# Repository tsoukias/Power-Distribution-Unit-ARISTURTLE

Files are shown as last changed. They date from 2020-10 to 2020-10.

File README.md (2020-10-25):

# Power Distribution Unit for Aristotle University Racing Team Electric (ARISTURTLE)

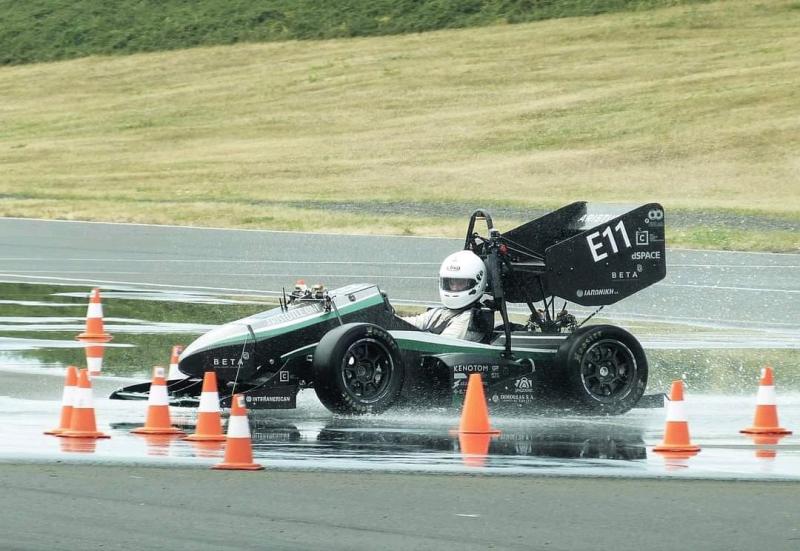
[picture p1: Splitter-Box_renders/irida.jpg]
<p align= "center">`</p>

In this repository anyone can found all the CAD files for the power distribution unit / splitter box used by ARISTURTLE in the electric racing car of 2017-2018, called Irida. This project was made in collaboration with Iakovos Koutris. 

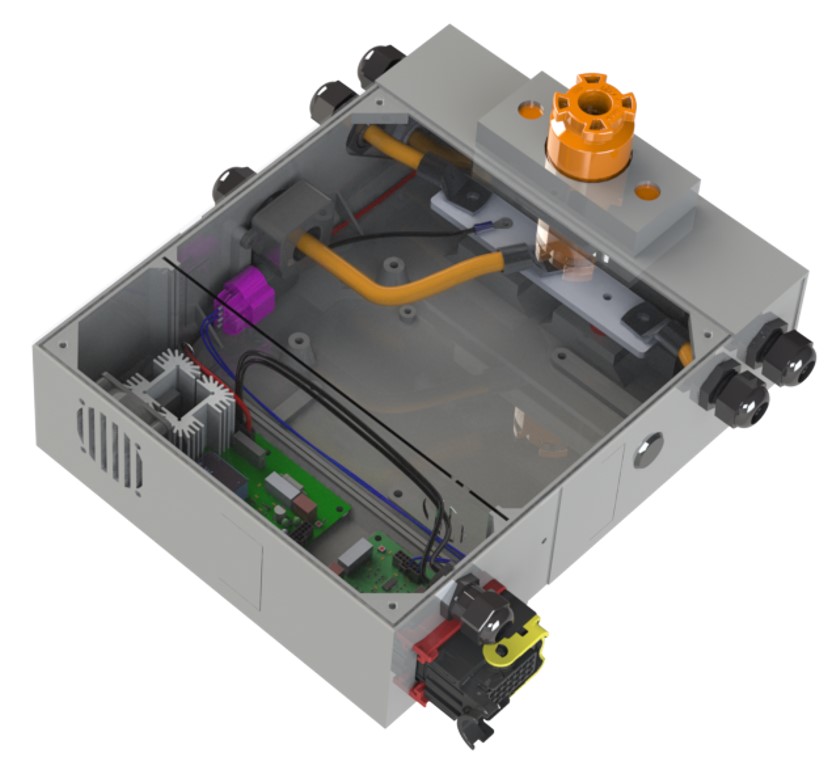
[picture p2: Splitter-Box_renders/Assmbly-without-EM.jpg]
<p align= "center">`</p>

### Brief Explanation

The power distribution unit is a *3D-printed box*, containing all the necessary connections for splitting the *DC High Voltage* from the battery of the racecar in order to supply the two inverters of the car, by splitting the positive and negative pole to two supply lines. It also contains the **discharge circuit** for the DC link capacitors of the inverters the **BSPD** (Brake System Plausibility Device), the **energy meter** for the Formula Student competitions and the **HVD** (High Voltage Disconnect). Below you can see the **powertrain** of the racecar. The top container is the *power distribution unit*.

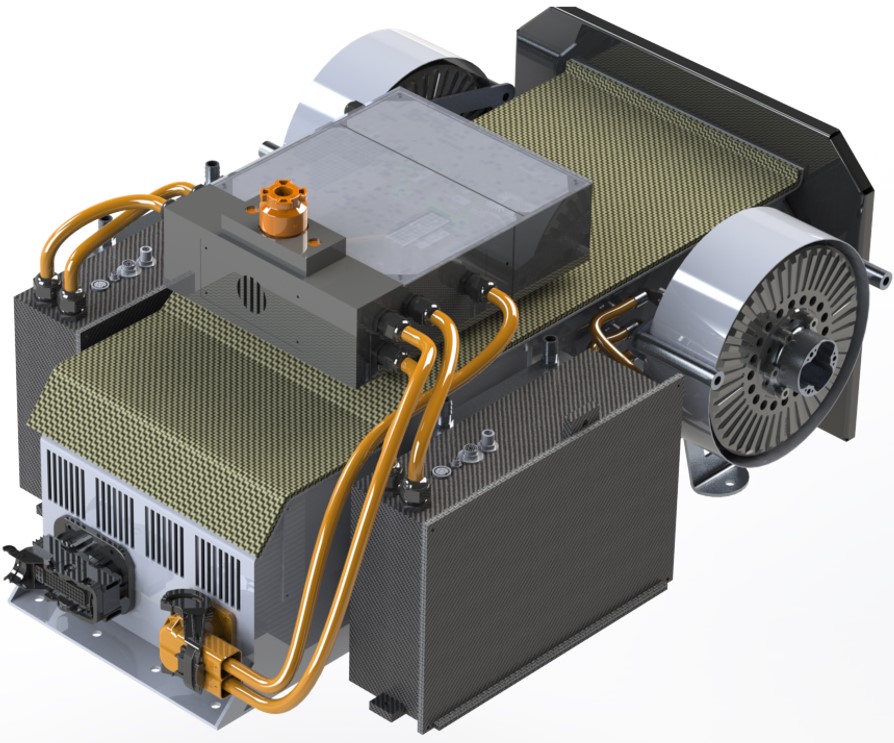
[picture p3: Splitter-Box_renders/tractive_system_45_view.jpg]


### Structural 

The power distribution unit is *3D-printed*, thing that gives facility for many configurations. The construction is composed of 6 pieces, due to the 3D printer restrictions, that were glued together. The box is made of ABS, due to its low weight, its high temperature resistance and because its electrically non conductive. An exploded view of the splitter box as well as the HVD lid can be seen below. The top lid of the box is a 2mm transparent polycarbonate piece for fast inspection of the system.  

| Splitter Box Exploded | HVD Lid |
| :---: | :---: |
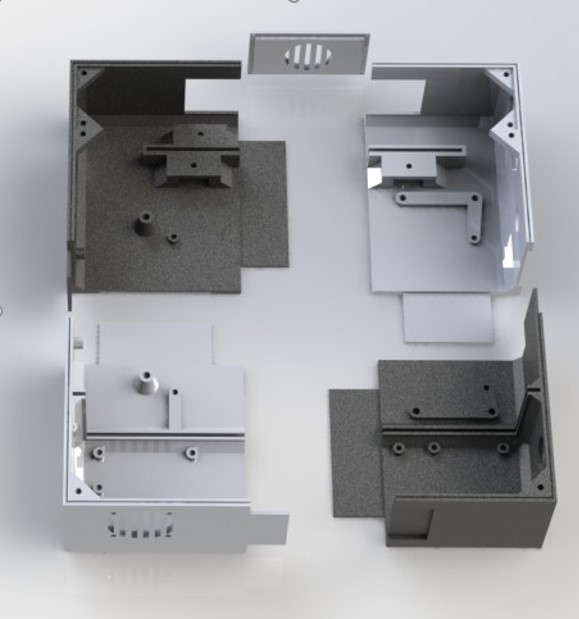
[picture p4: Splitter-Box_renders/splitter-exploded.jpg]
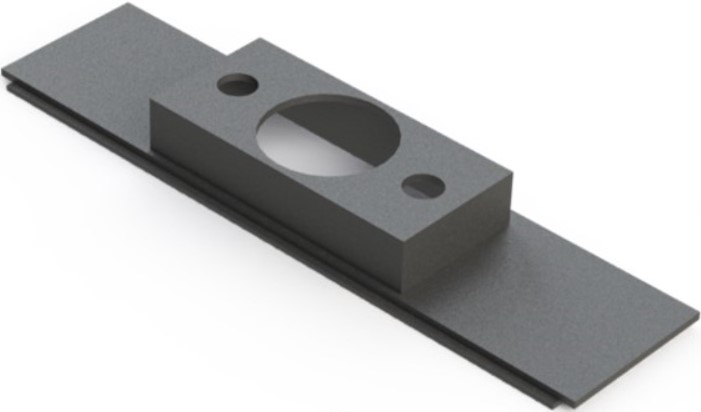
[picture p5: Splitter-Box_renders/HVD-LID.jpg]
|  |  |

For waterproofing the construction a special recess was placed around the perimeter of the box for installing an o-ring. The box has two compartments that are separated by a polycarbonate piece for ensuring electrical insulation between the two. One other important aspect of the construction is the use of brass threaded inserts for screwing all the components together. These were fitted to ABS via a soldering iron. Lastly, for ensuring proper installation for the High Voltage path threaded insulators were used. 

| Brass Threaded Insert | Threaded Insulators |
| :---: | :---: |
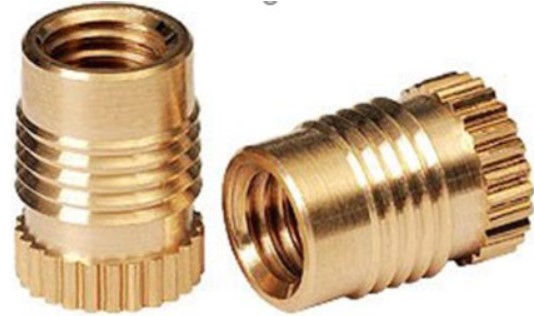
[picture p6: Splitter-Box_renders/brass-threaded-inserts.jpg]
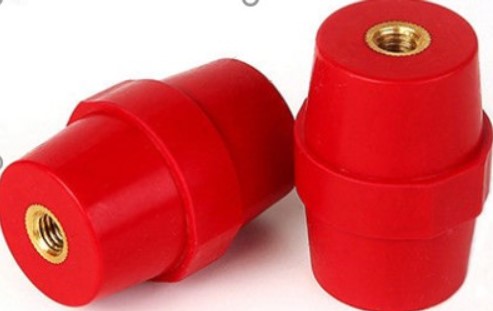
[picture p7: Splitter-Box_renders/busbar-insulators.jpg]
|  |  |

### High Voltage Compartment

The High Voltage compartment features the two nodes where the positive and negative terminal of the battery split, the HVD, the Energy Meters & also topologies for current and voltage measurements. The nodes can be seen below for each terminal:

| HV+ busbar | HV- busbar |
| :---: | :---: |
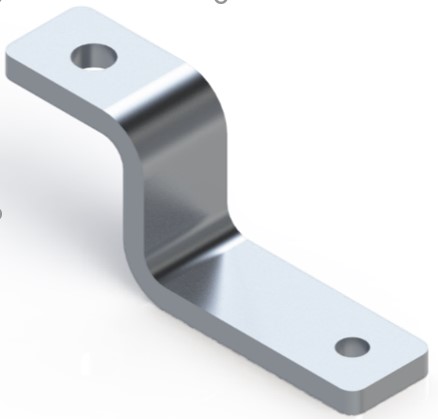
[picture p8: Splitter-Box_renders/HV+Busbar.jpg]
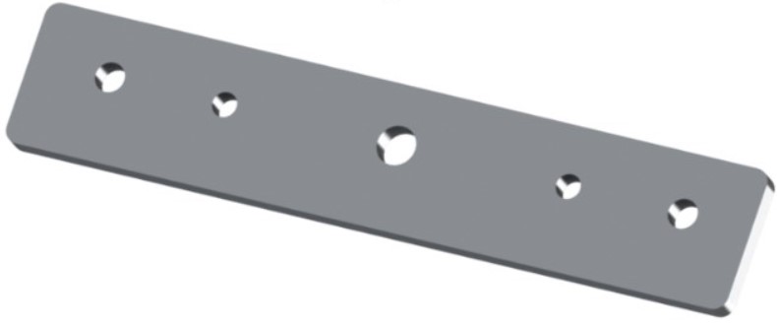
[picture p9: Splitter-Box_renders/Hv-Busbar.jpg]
|  |  |

The HVD is placed in the front part of the box, right in the center. It is contained inside a lid, that is mounted on the top of the box, and is mounted in the outside skin of the chassis with two M8 bolts. 

Two cables from the accumulator container are inserting the splitter box from the left side through PG13.5 cable glands as shown in the picture.

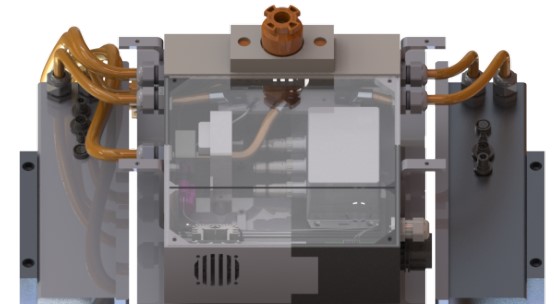
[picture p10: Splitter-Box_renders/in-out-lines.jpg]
<p align= "center">`</p>

The positive line is connected to the one side of the HVD with a 35M8 ring terminal. The other side of the HVD is where the split takes place, as an S shaped HV+ busbar and a 25M8 ring terminal is connected there. The busbar is then connected to a 25M6 ring terminal and the cable exits the splitter box from the left side through a cable gland, while the other cable exits from the right side. 

The negative line passes through a LEM that is mounted in the side of the box and is connected in the middle of the HV- busbar with a 35M8 ring terminal. Then from the end of each side, a 25M6 ring terminal is connected and the cables are exiting the splitter box through PG 13.5 cable glands.

| Cable gland | Ring Terminal |
| :---: | :---: |
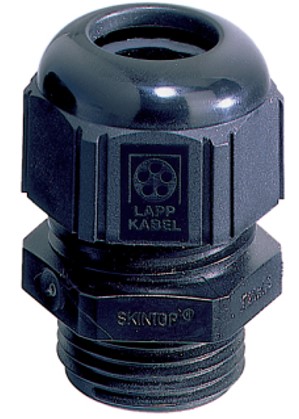
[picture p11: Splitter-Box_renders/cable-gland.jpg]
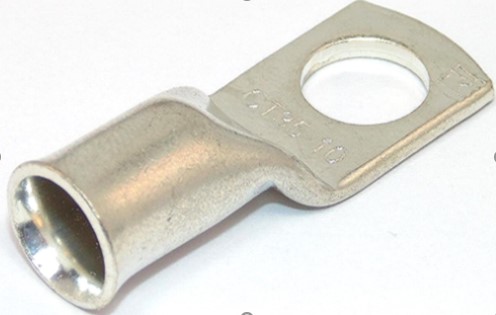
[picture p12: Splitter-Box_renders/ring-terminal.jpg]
|  |  |

The HV+ and HV- busbars are also separated by a 2mm polycarbonate piece and are supported by cylindrical busbar insulators that have screw thread from both sides. In front of the HV- busbar there is enough space to accommodate the different energy meters of the competitions as well as configurations with brass threaded inserts to mount them in the floor.

### Low Voltage Compartment

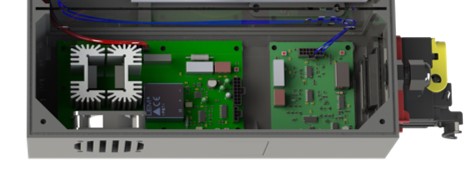
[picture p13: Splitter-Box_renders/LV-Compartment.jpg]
<p align= "center">`</p>

The Low Voltage Compartment consists of the discharge and BSPD PCB, a fan and a connector. The discharge PCB is susceptible to heat, thus a heat sink along with a fan is used. Airflow is achieved using grilles at the position of the fan, at the polycarbonate wall between the HV and LV compartment and also at the very front of the box (at the HV+ side) of the power distribution unit. M3 threaded inserts are used to mount the PCBs.  All the signals for and from the PCBs communicate through a 21-pin connector. Above the connector there is a PG 9 cable gland for the cables of the measuring points.

| BSPD | Discharge |
| :---: | :---: |
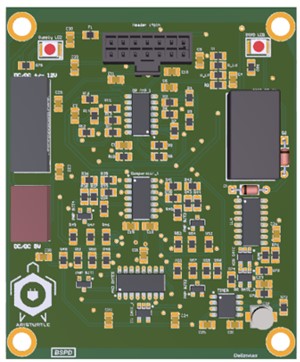
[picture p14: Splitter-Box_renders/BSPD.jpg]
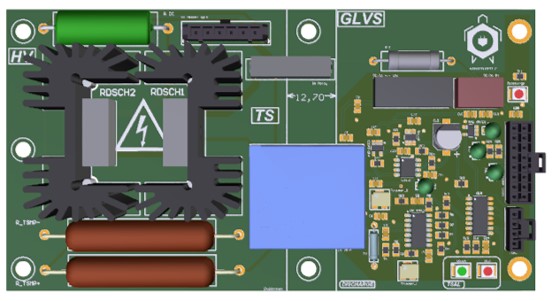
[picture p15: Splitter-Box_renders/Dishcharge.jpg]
|  |  |

### Mounting 

The splitter box is located in the middle of the rear part of the chassis, above the accumulator container and just behind the driver’s seat. It is accessible from the top part of the chassis for the easy insertion/removal of the energy meters during the competitions and is supported by an aluminum mounting that is screwed on the chassis.

| Mounting | Top View |
| :---: | :---: |
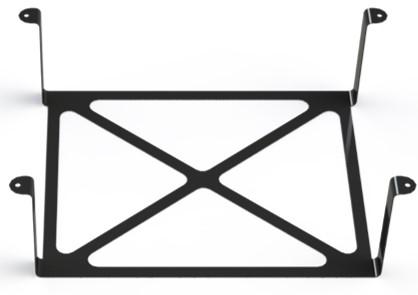
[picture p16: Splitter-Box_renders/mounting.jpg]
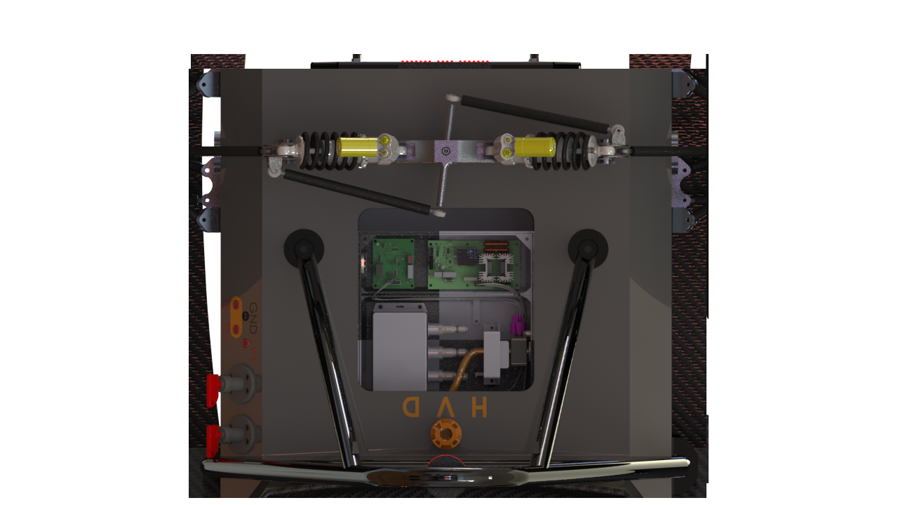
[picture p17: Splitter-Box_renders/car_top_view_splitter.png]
|  |  |

The position of the splitter box is shown in the picture below.

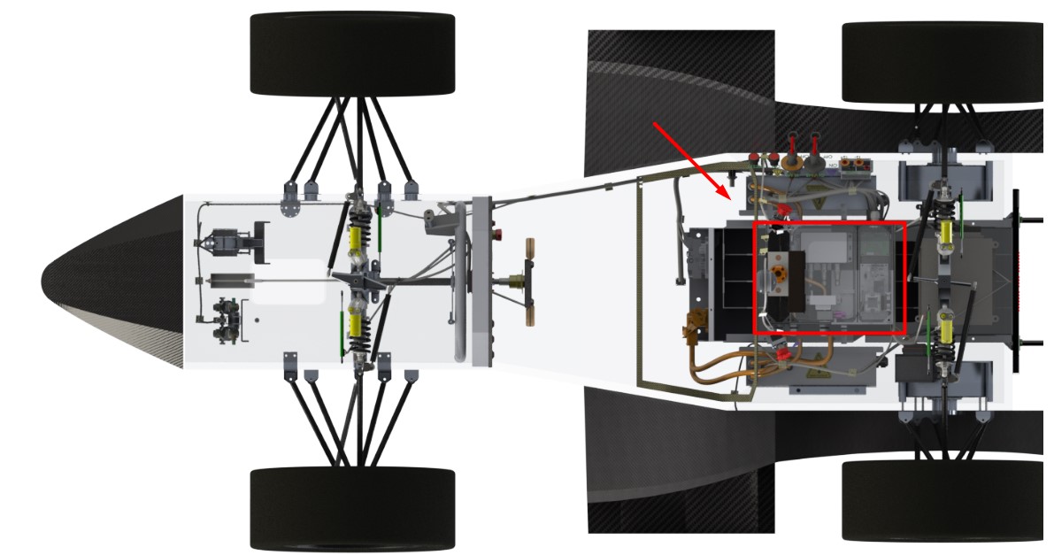
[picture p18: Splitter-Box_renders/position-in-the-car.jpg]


### Energy Meters

The team participated to FS ATA Italy, FS East and FS Czech Republic and each one of them had a different energy meter for the measurement of the consumed energy. Below you can see the three different topologies. 

##### FS ATA 

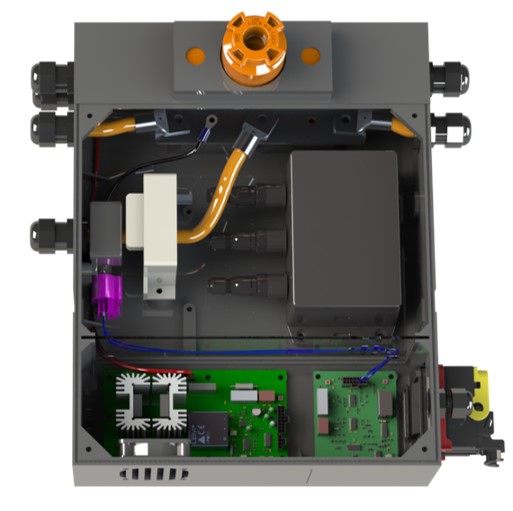
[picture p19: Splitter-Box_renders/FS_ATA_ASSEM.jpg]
<p align= "center">`</p>

##### FS EAST

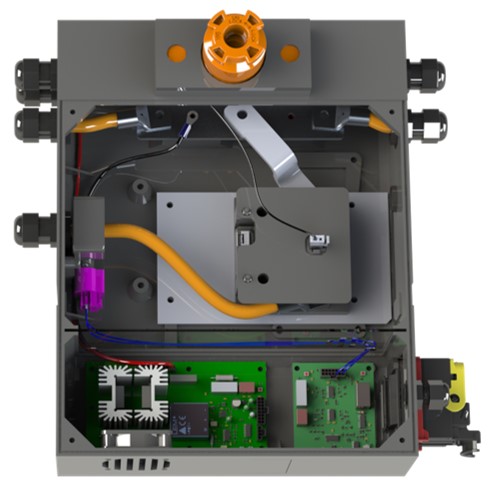
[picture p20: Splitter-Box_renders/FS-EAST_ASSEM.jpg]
<p align= "center">`</p>

##### FS CZECH REPUBLIC

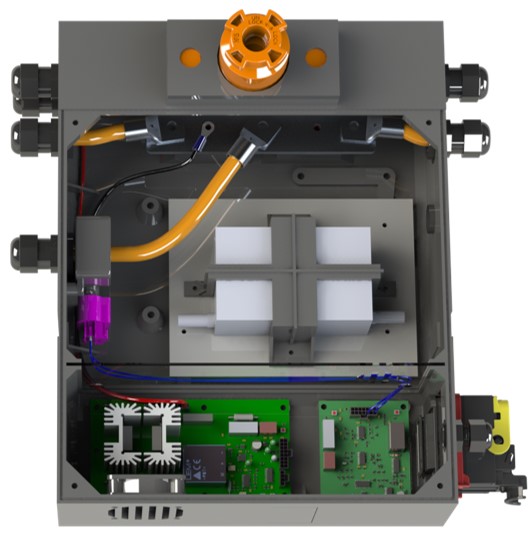
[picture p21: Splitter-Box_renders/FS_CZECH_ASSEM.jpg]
<p align= "center">`</p>

### Notice 

For any further details about the design feel free to contact me to: stefanostsoukias@gmail.com

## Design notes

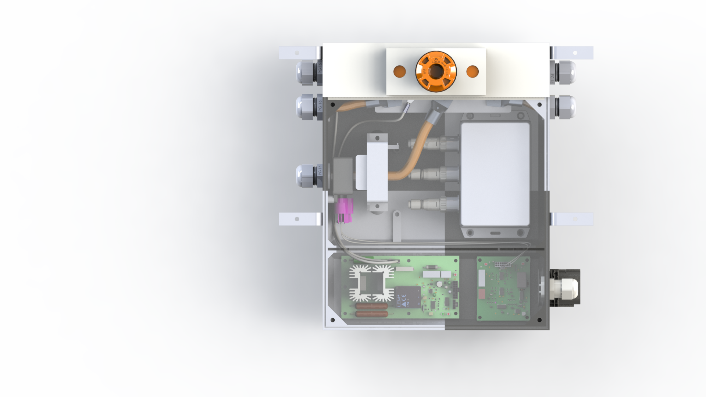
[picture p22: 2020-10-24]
Splitter-Box_renders/fsata_splitter.png

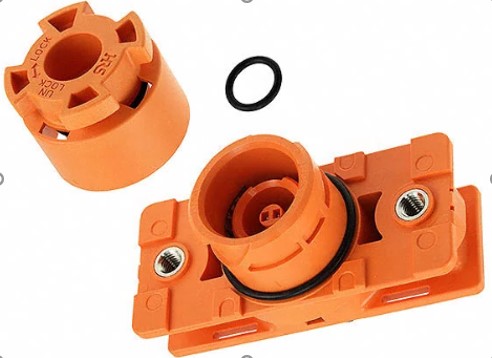
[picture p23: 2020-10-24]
Splitter-Box_renders/HVD.jpg

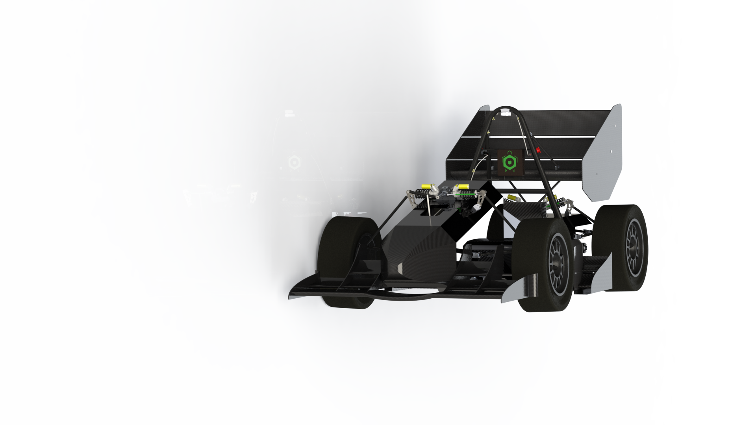
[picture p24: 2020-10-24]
Splitter-Box_renders/front car.png

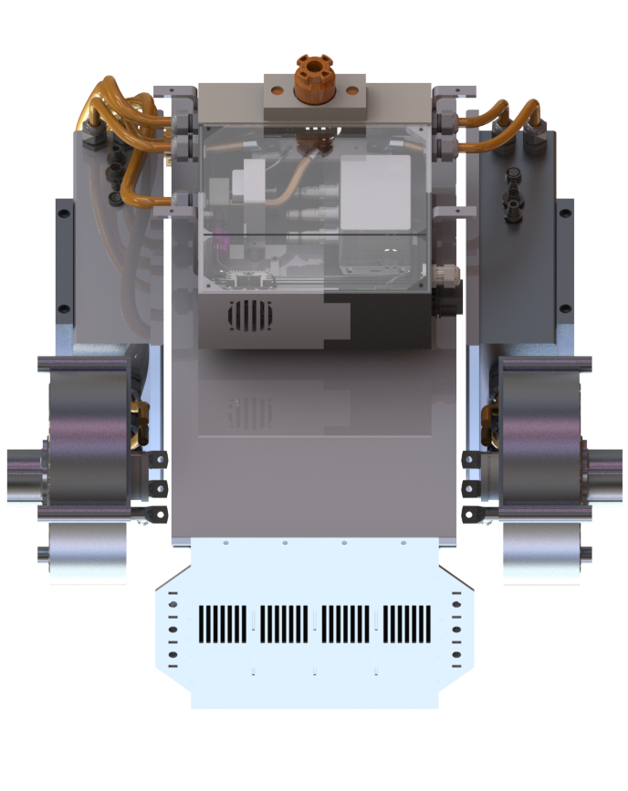
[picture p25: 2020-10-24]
Splitter-Box_renders/Tractive_system_HV_without_backlid-Cropped.png

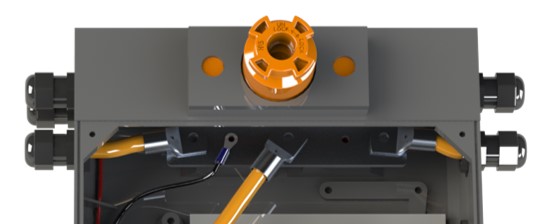
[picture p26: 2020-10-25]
Splitter-Box_renders/HV-connection.jpg

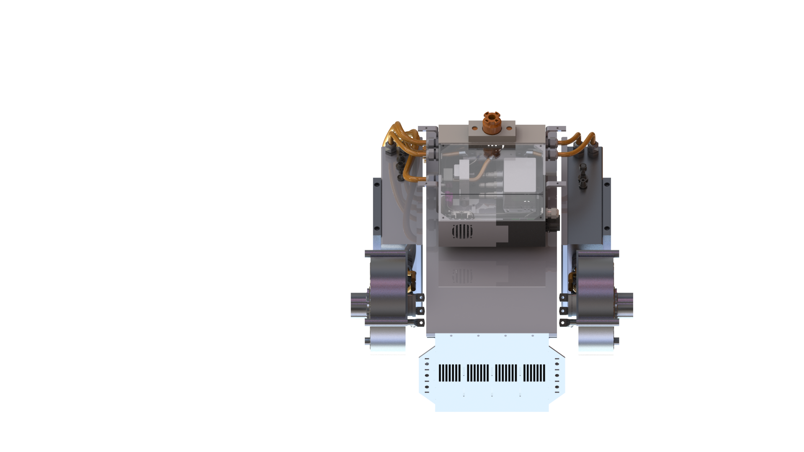
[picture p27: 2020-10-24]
Splitter-Box_renders/Tractive_system_HV_without_backlid.png

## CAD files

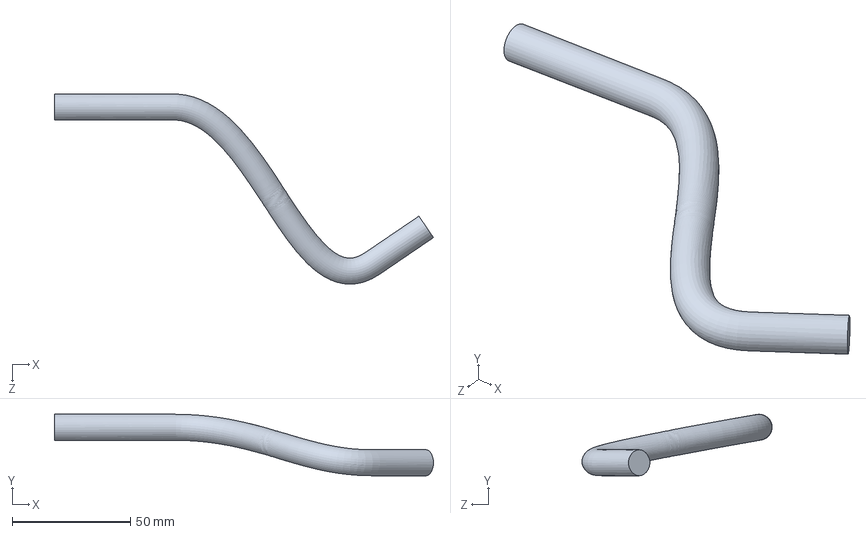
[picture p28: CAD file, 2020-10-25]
Splitter Box CAD/Cable_12-boxassembly.sldasm
160.1 x 26.0 x 80.4 mm

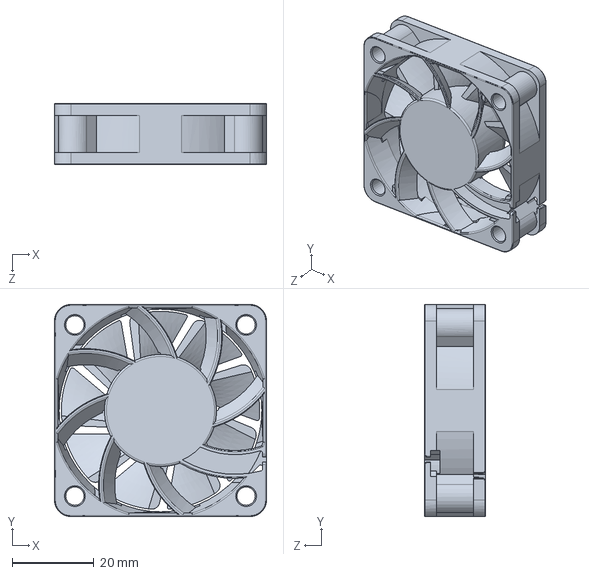
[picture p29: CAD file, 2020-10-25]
Splitter Box CAD/San_Ace_DC_52GA15_RD.SLDPRT
52.0 x 52.0 x 15.0 mm

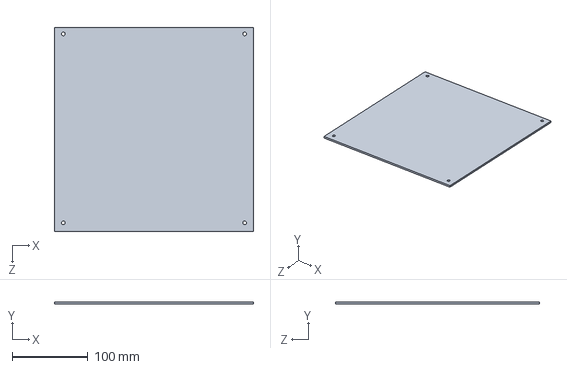
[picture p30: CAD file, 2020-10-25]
Splitter Box CAD/lid polycarbonate.SLDPRT
262.0 x 3.00 x 269.0 mm

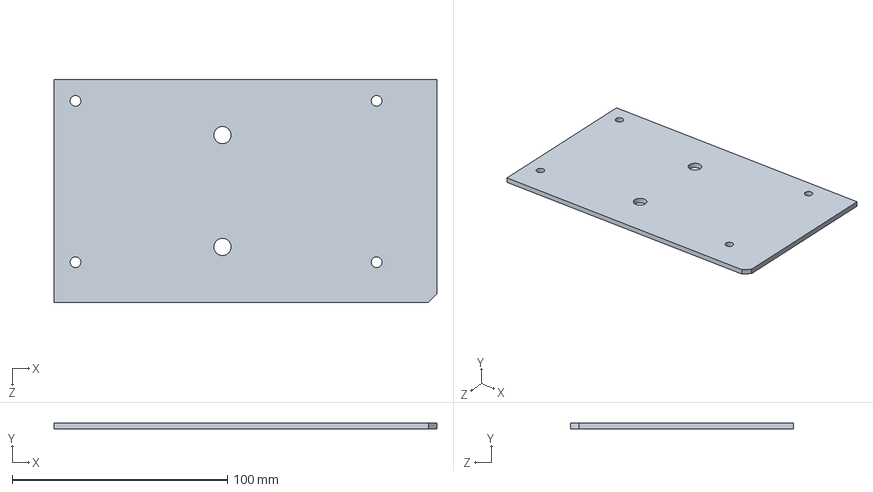
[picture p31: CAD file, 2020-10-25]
Splitter Box CAD/fseastpseudo.SLDPRT
178.1 x 3.00 x 103.8 mm

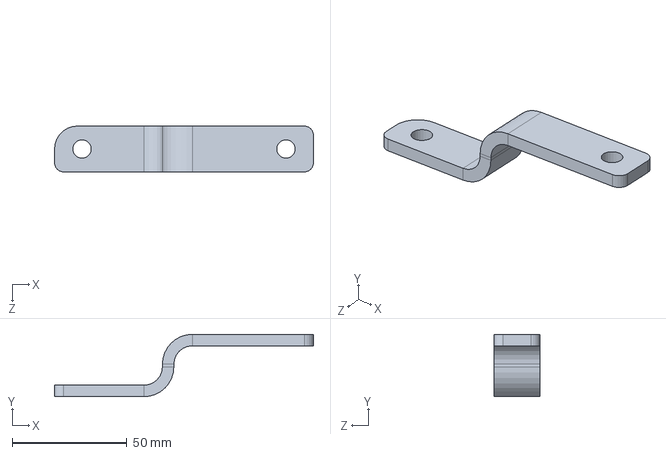
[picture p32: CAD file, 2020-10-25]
Splitter Box CAD/lamakieast.SLDPRT
112.8 x 27.1 x 20.0 mm

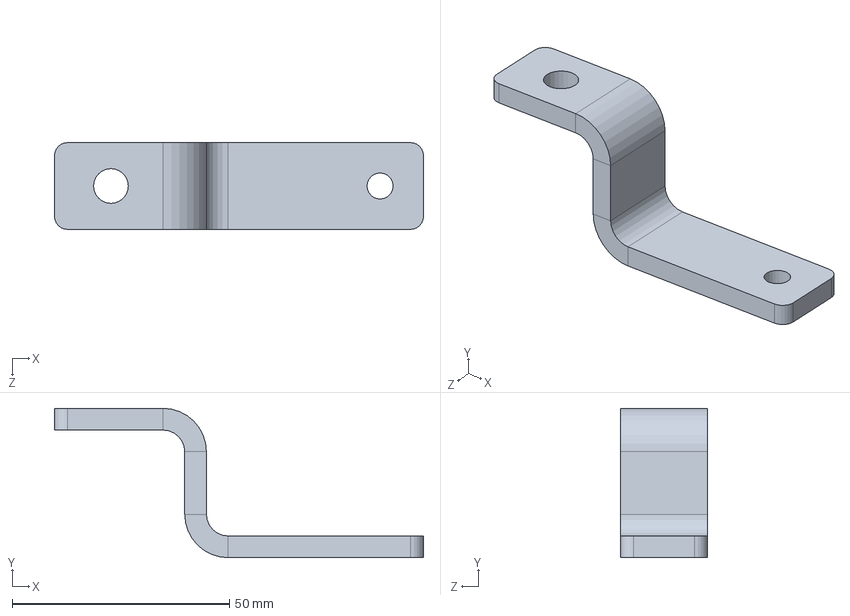
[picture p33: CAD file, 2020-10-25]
Splitter Box CAD/lamakiHV+.SLDPRT
85.0 x 34.4 x 20.0 mm

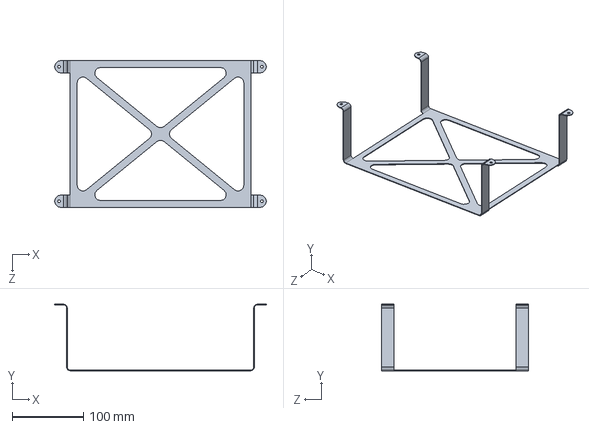
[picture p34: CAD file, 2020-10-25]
Splitter Box CAD/SplitterBoxMounting.SLDPRT
297.9 x 93.5 x 207.0 mm

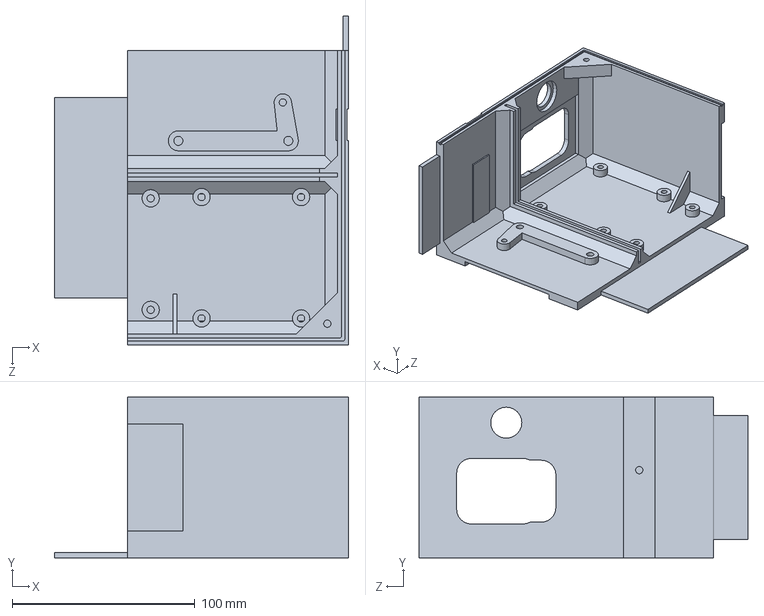
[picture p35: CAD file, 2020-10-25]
Splitter Box CAD/Bbottomright.SLDPRT
161.0 x 88.0 x 180.0 mm

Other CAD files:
Splitter Box CAD/Cable_9-boxassembly.sldasm
Splitter Box CAD/Cable_8-boxassembly.sldasm
Splitter Box CAD/Cable_3-boxassembly.sldasm
Splitter Box CAD/Cable_2-boxassembly.sldasm
Splitter Box CAD/Cable_5-boxassembly-001.sldasm
Splitter Box CAD/Cable_1-boxassembly-001.sldasm
Splitter Box CAD/Cable_7-boxassembly.sldasm
Splitter Box CAD/Cable_10-boxassembly.sldasm
Splitter Box CAD/Cable_11-boxassembly-001.sldasm
Splitter Box CAD/Cable_6-boxassembly.sldasm
Splitter Box CAD/21PosCnctr.SLDPRT
Splitter Box CAD/21PosHeader.SLDPRT
Splitter Box CAD/21PosSlide.SLDPRT
Splitter Box CAD/Bbottomleft.SLDPRT
Splitter Box CAD/Btopleft.SLDPRT
Splitter Box CAD/Btopright.SLDPRT
Splitter Box CAD/Cable-Lug-KRF.SLDPRT
Splitter Box CAD/EnergyMeter_ATA.SLDPRT
Splitter Box CAD/FSCzech energy meter.SLDPRT
Splitter Box CAD/HV+.SLDPRT
Splitter Box CAD/HV+HV-.SLDPRT
Splitter Box CAD/HVD-EM30MSD.sldprt
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
